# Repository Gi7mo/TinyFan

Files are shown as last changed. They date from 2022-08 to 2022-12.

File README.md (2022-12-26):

# Klipper TinyFan

### Navigation:
|[• Installation & Klipper](./Klipper)|[• Get a PCB](./PCB)|[• Mounts](./STL)|
|---|---|---|

|[• CAD Files](./CAD)|[• Manual](./TinyFan_Pinout.pdf)|[• Pictures](./Images)|
|---|---|---|
<br>

**ATTENTION**<br>
The LDO is flipped in the image, please don't mount it with the fin outward the pcb<br>
it must be mounted inward, so 180° flipped to shown in the image
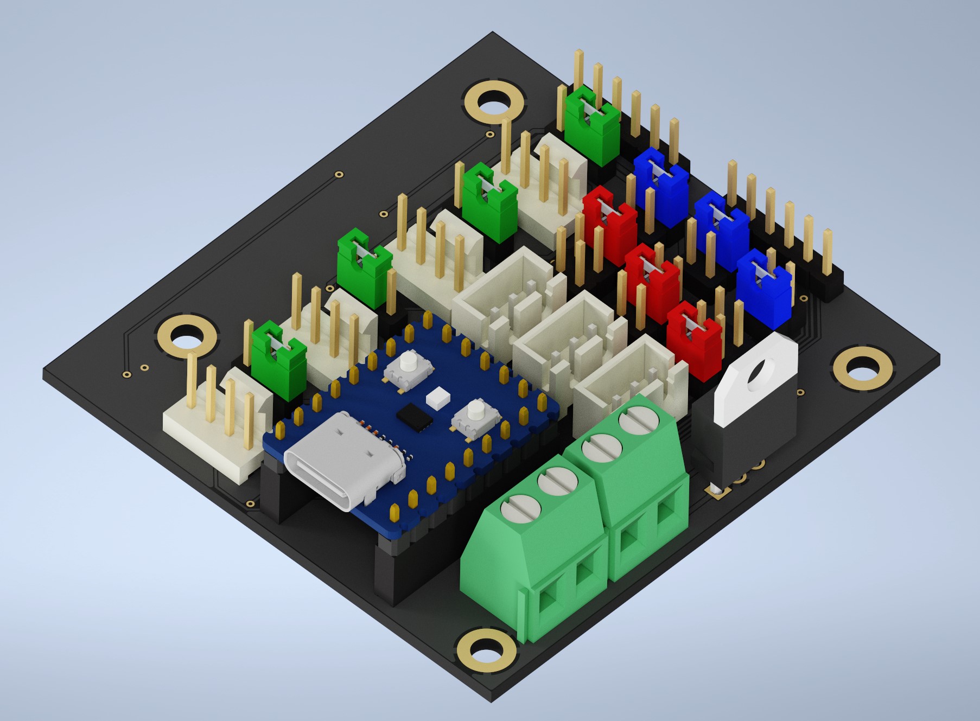
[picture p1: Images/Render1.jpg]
PCB

<br>

## Notes
- Many thanks to [Rama](https://github.com/Ramalama2) who came up with the initial idea and supported me a lot.
- You can contact me via Discord "Gi7mo!#4618"
- This project does not come with any warranty, if you choose to build/use one, you are doing this at your own risk!

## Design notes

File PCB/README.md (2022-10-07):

## TinyFan PCB Sources:
- KiCad Folder: Sources
- ProductionFiles Folder: Gerber, PNP & BOM for ordering.

## BOM:
|Reference |Quantity|Value |LCSC |Ali|
|---|---|---|---|-----|
|5VIN1 24VIN1 |2 |Conn_01x02 |C475092 |[Link](https://s.click.aliexpress.com/e/_DC1TC2L)|
|AUX1 AUX2 AUX3 |3 |Conn_01x03 |C144394 |[Link](https://s.click.aliexpress.com/e/_DEyuBIn)|
|AUX1PWR1 AUX2PWR1 AUX3PWR1 |3 |Conn_02x03_Odd_Even|C492420 |[Link](https://s.click.aliexpress.com/e/_DDO0FkL)|
|C1 C2 |2 |10pF |C107172 |[Link](https://s.click.aliexpress.com/e/_DkweKyn)|
|FAN1 FAN2 FAN3 FAN4 |4 |Conn_01x04 |C402778 | |
|FAN1PWR1 FAN2PWR1 FAN3PWR1 FAN4PWR1 |4 |Conn_01x03 |C2937625|[Link](https://s.click.aliexpress.com/e/_DDO0FkL)|
|J1 J2 J3 |3 |Conn_02x02_Odd_Even|C706892 |[Link](https://s.click.aliexpress.com/e/_DDO0FkL)|
|J4 J5 |2 |Conn_01x06_Male |C492405 |[Link](https://s.click.aliexpress.com/e/_DDO0FkL)|
|Q1 Q2 Q3 Q4 |4 |BSS138 |C52895  |[Link](https://s.click.aliexpress.com/e/_DF4Oc0f)|
|Q8 Q9 Q10 |3 |wsf3085 |C148428 |[Link](https://s.click.aliexpress.com/e/_DlBoAQT)|
|R1 R2 R3 R4 R5 R6 R7 R8 R15 R16 R17 |11 |10K |C144471 |[Link](https://s.click.aliexpress.com/e/_Ddns0gR)|
|U1 |1 |L7812 |C105651 |[Link](https://s.click.aliexpress.com/e/_DdftV8F)|
|RP2040 9Pin Female Headers |2 |9 |C39576  |[Link](https://s.click.aliexpress.com/e/_DdUyVnt)|
|RP2040 5Pin Female Headers |1 |5 |C50950  |[Link](https://s.click.aliexpress.com/e/_DFuppTv)|

Additional a [RP2040-Zero](https://s.click.aliexpress.com/e/_DFCoOxH)

**Assembly**
- Order the pcb at e.g. [pcbway](https://www.pcbway.com/project/shareproject/Voron_TinyFan_Adapter_1928b94a.html) or [jlcpcb](https://jlcpcb.com/)
- Order the parts at e.g. [lcsc](https://www.lcsc.com/)

**ATTENTION**<br>
The LDO is flipped in the image, please don't mount it with the fin outward the pcb<br>
it must be mounted inward, so 180° flipped to shown in the image
- PCB

## Notes
- This readme file contains Amazon Associate, Aliexpress affiliate, PCBWay affiliate links. I make a comission on qualifying purchases.

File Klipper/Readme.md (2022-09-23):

## Klipper:
<br>

<ul><li><details>
<summary><h3><a href="./TinyFan.cfg">TinyFan Example Config</a></h></summary>
</details></li></ul>

<ul><li><details>
<summary><h3>Board Aliases:</h></summary>
<pre>[mcu tinyfan]<br>serial: /dev/serial/by-id/usb-Klipper_rp2040_XXXXXXXXXXXX<br>restart_method: command<br><br>[board_pins tinyfan]<br>mcu: tinyfan<br>aliases:<br>	#FAN Ports:<br>	FAN1_PWM=gpio0, FAN1_RPM=gpio7,<br>	FAN2_PWM=gpio1, FAN2_RPM=gpio8,<br>	FAN3_PWM=gpio2, FAN3_RPM=gpio9,<br>	FAN4_PWM=gpio3, FAN4_RPM=gpio10,<br>	<br>	#AUX Ports:<br>	AUX1_PWM=gpio4, AUX1_RPM=gpio26,<br>	AUX2_PWM=gpio5, AUX2_RPM=gpio27,<br>	AUX3_PWM=gpio6, AUX3_RPM=gpio28,<br>	<br>	#GPIO Header:<br>	G1=gpio29, G2=gpio11, G3=gpio12,<br>	G4=gpio13, G5=gpio14, G6=gpio15,<br>	<br>	#Waveshare LED:<br>	LED=gpio16</pre>
</details></li></ul>

<ul><li>
<details>
 <summary><h3>Installation Steps:</h></summary>
 <li>ssh into your raspberry pi</li>
 <li>stop the klipper service <code>sudo systemctl stop klipper</code></li>
 <li>run <code>ls /dev</code> and keep the list open</li>
 <li>Connect the rp2040 to your raspberry while holding down the boot button</li>
 <li>run again <code>ls /dev</code> and look out for the added device, usually this is sda1</li>
 <li>chroot into your klipper directory <code>cd klipper</code></li>
 <li>cleanup all previous build files <code>make clean</code></li>
 <li>create a new build config <code>make menuconfig</code></li>
 <li>using the following settings</li>
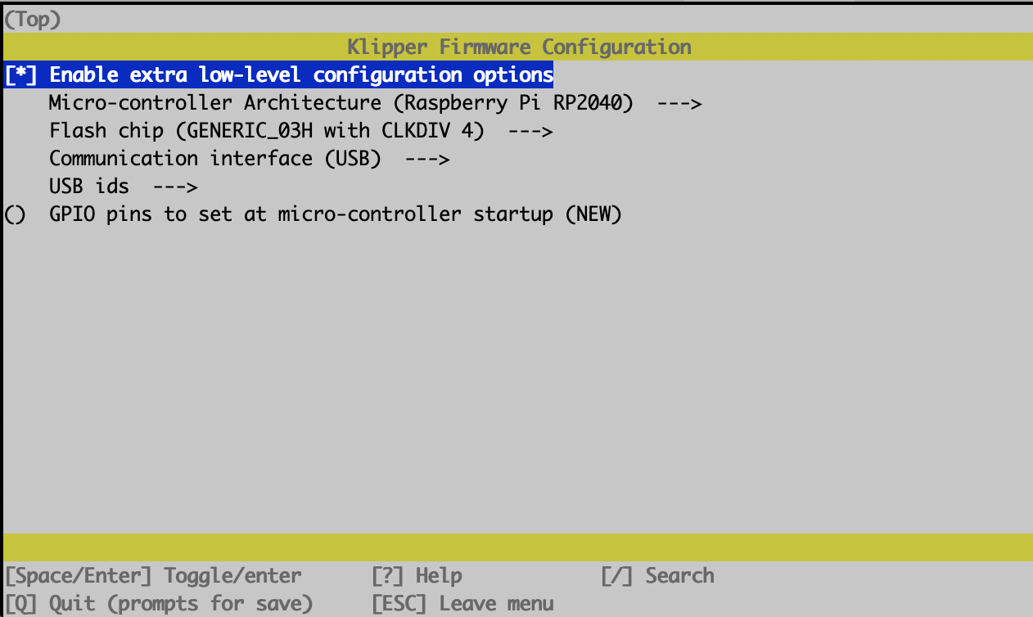
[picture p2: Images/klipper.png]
 
 <li>run the build <code>make</code></li>
 <li>copy the firmware onto the rp2040</li>
 <pre>sudo mount /dev/sda1 /mnt<br>sudo cp out/klipper.uf2 /mnt<br>sudo umount /mnt</pre>
 <li>find your mcu address by running <code>ls /dev/serial/by-id/*</code></li>
 <li>add the new mcu to your printer.cfg</li>
 <pre>[mcu fans]<br>serial: /dev/serial/by-id/usb-Klipper_rp2040_XXXX</pre>
 <li>start the klipper service <code>sudo systemctl start klipper</code></li>
</details></li></ul>

<ul><li>
<details>
 <summary><h3>Alternative Installation:</h></summary>
 <li>ssh into your raspberry pi</li>
 <li>Connect the rp2040 to your raspberry while holding down the boot button</li>
 <li>stop the klipper service <code>sudo systemctl stop klipper</code></li>
 <li>chroot into your klipper directory <code>cd klipper</code></li>
 <li>cleanup all previous build files <code>make clean</code></li>
 <li>create a new build config <code>make menuconfig</code></li>
 <li>using the following settings</li>
 
 <li>run the build <code>make</code></li>
 <li>run <code>make flash FLASH_DEVICE="2e8a:0003"</code></li>
 <li>find your mcu address by running <code>ls /dev/serial/by-id/*</code></li>
 <li>add the new mcu to your printer.cfg</li>
 <pre>[mcu fans]<br>serial: /dev/serial/by-id/usb-Klipper_rp2040_XXXX</pre>
 <li>start the klipper service <code>sudo systemctl start klipper</code></li>
</details>
</li></ul>

<ul><li>
<details>
 <summary><h3>Outputs and Options:</h></summary>
 <details>
  <summary><h4>Fan1, Fan2, Fan3 and Fan4 are PWM Fans with RPM Output and selectable Voltage for 12 and 24V</h></summary>
  <pre>[fan_generic tinyfan_fan1]<br>pin: tinyfan:FAN1_PWM<br>tachometer_pin: ^tinyfan:FAN1_RPM<br>hardware_pwm: true<br>cycle_time: 0.00004<br><br>[fan_generic tinyfan_fan2]<br>pin: tinyfan:FAN2_PWM<br>tachometer_pin: ^tinyfan:FAN2_RPM<br>hardware_pwm: true<br>cycle_time: 0.00004<br><br>[fan_generic tinyfan_fan3]<br>pin: tinyfan:FAN3_PWM<br>tachometer_pin: ^tinyfan:FAN3_RPM<br>hardware_pwm: true<br>cycle_time: 0.00004<br><br>[fan_generic tinyfan_fan4]<br>pin: tinyfan:FAN4_PWM<br>tachometer_pin: ^tinyfan:FAN4_RPM<br>hardware_pwm: true<br>cycle_time: 0.00004</pre>
 </details>
 • Be aware that the 12V rail is only capable of a max of 1.5A<br>• Aux1, Aux2 and Aux3 are more versatile
<s>Adding more Thermistors</s>
 <details>
  <summary><h4>Driving more 5V, 12V and 24V Fans</h></summary>
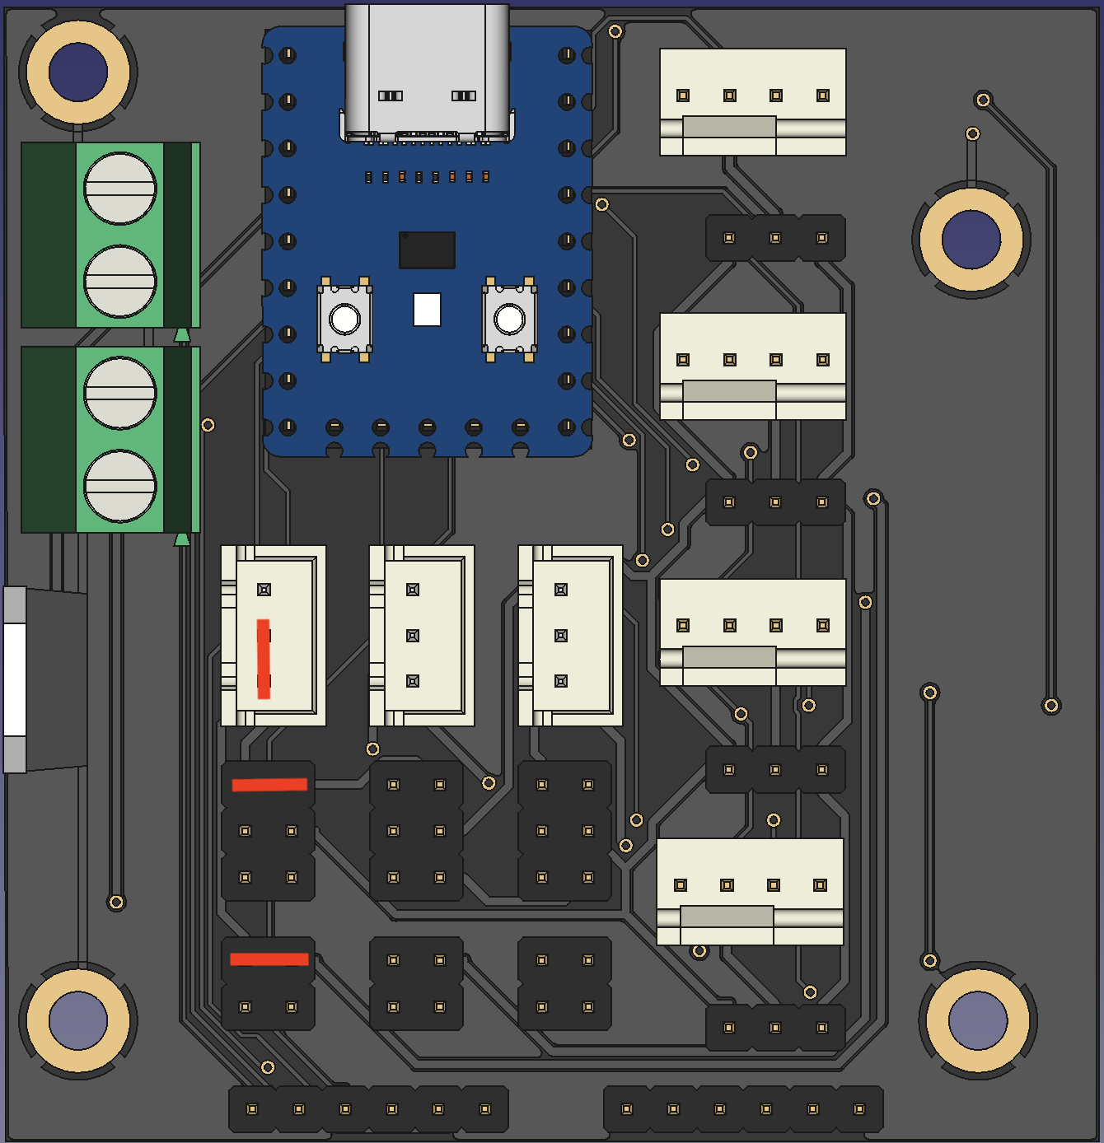
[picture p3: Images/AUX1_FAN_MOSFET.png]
  
  <pre>[fan_generic tinyfan_aux1]<br>pin: tinyfan:AUX1_PWM<br>hardware_pwm: true<br>cycle_time: 0.00004<br><br>[fan_generic tinyfan_aux2]<br>pin: tinyfan:AUX2_PWM<br>hardware_pwm: true<br>cycle_time: 0.00004<br><br>[fan_generic tinyfan_aux2]<br>pin: tinyfan:AUX3_PWM<br>hardware_pwm: true<br>cycle_time: 0.00004</pre>
 </details>
 <details>
  <summary><h4>Driving 5V, 12V and 24V Leds</h></summary>
  
  <pre>[output_pin aux1_blue]<br>pin: tinyfan:AUX1_PWM<br>pwm: True<br>cycle_time: 0.0005<br>hardware_pwm: true<br><br>[output_pin aux2_red]<br>pin: tinyfan:AUX2_PWM<br>pwm: True<br>cycle_time: 0.0005<br>hardware_pwm: true<br><br>[output_pin aux3_green]<br>pin: tinyfan:AUX3_PWM<br>pwm: True<br>cycle_time: 0.0005<br>hardware_pwm: true</pre>
 </details>
 <details>
  <summary><h4>Driving Neopixels</h></summary>
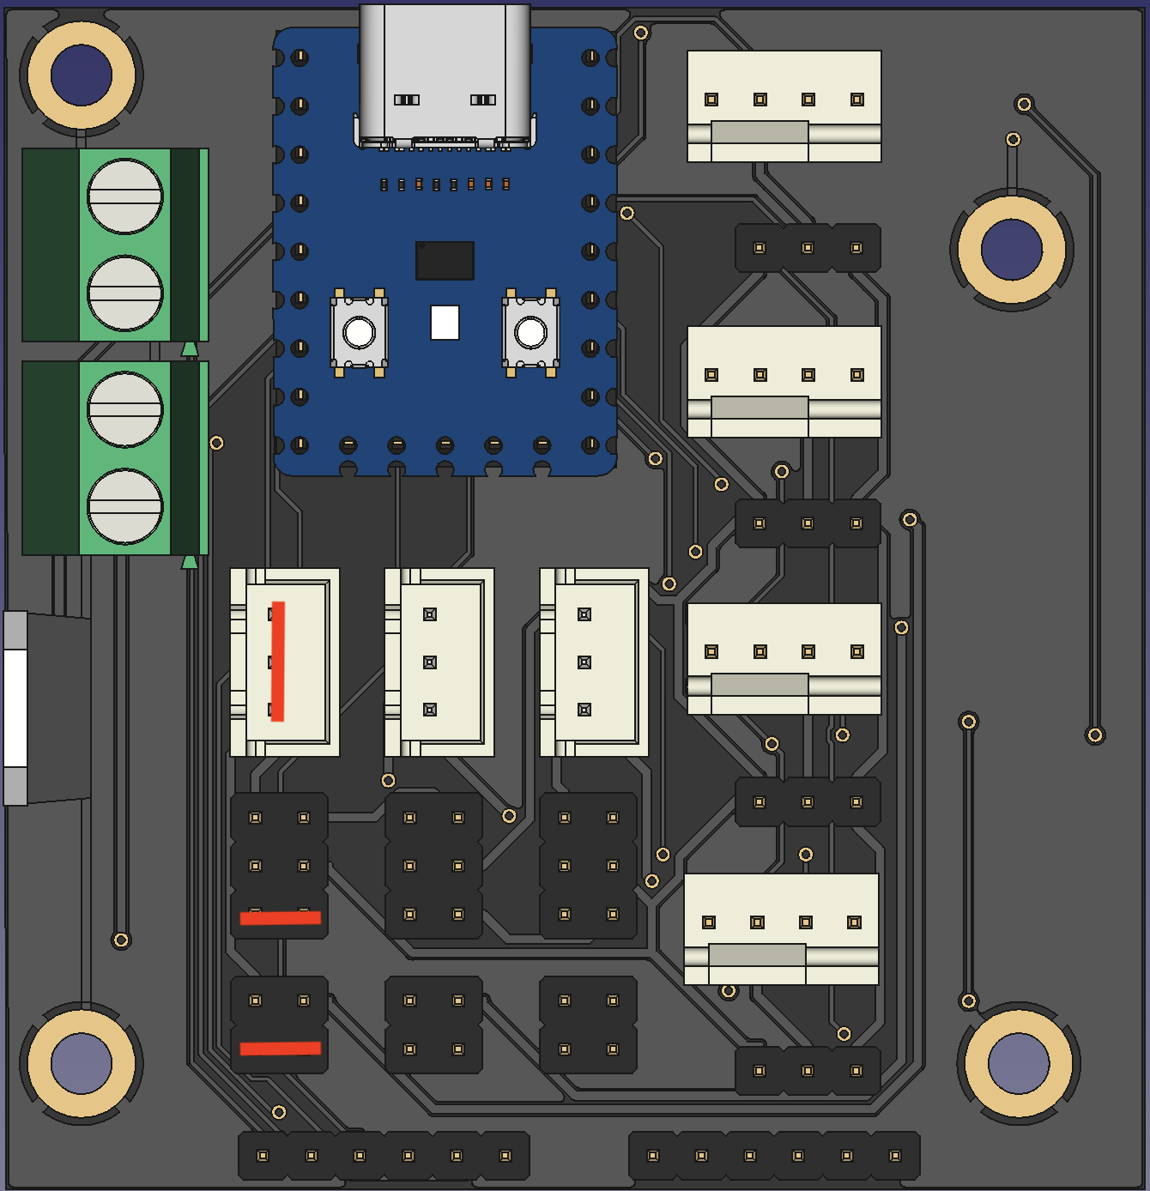
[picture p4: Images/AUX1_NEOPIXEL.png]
  
  <pre>[neopixel fan_neopixels]<br>pin: tinyfan:AUX1_RPM<br>chain_count: 18</pre>
 </details>
</details>
</li></ul>
<ul><li><details>
 <summary><h3>Pinout and Options (Picturized):</h></summary>
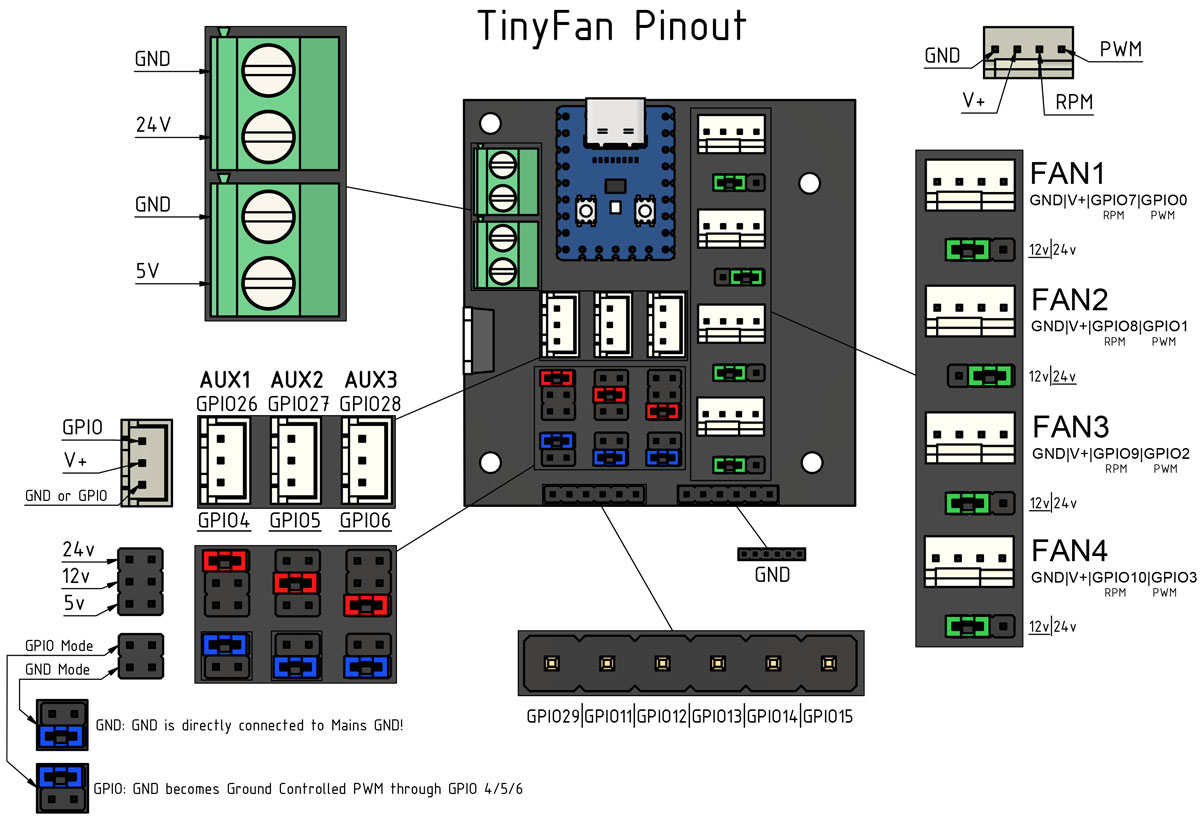
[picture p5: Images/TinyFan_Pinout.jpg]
 
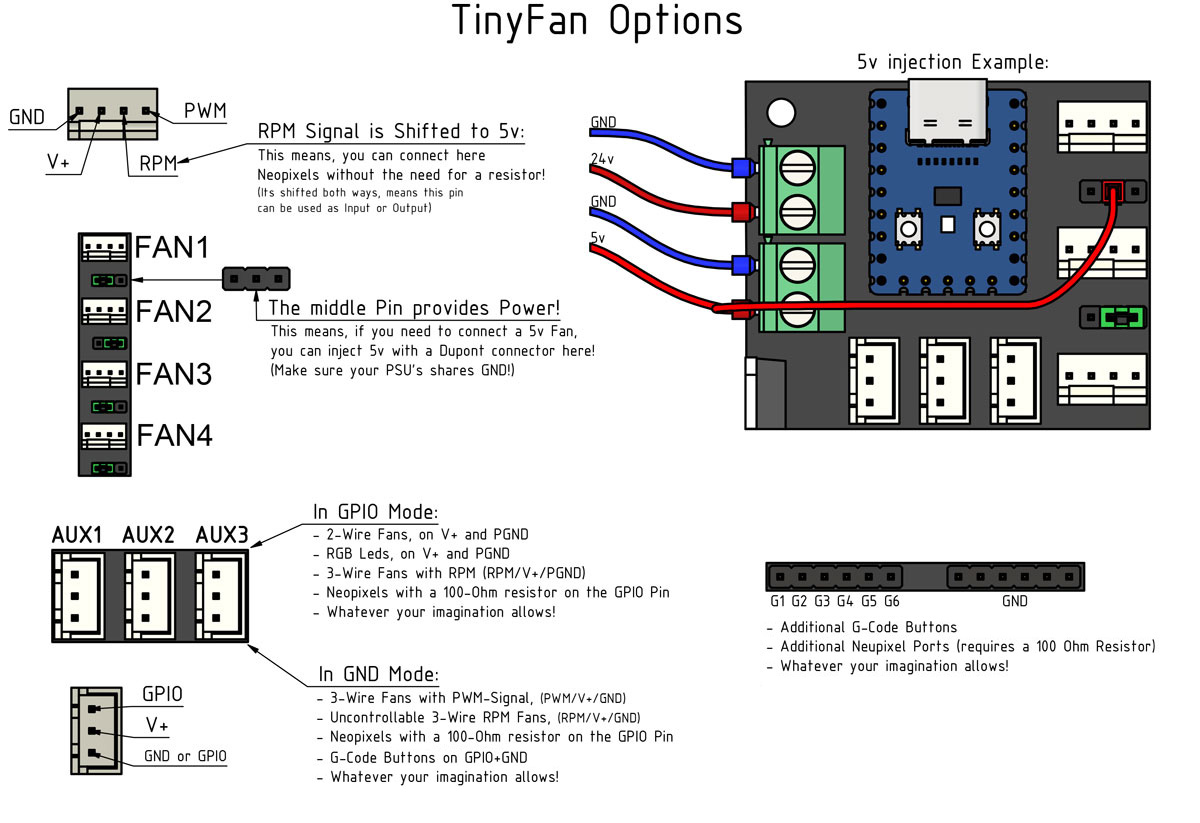
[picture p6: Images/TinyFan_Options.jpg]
 
</details></li></ul>

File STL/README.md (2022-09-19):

## Extrusion Mount:
- Folderstructure: Extrusion_DEGREE
- You can decide in which rotation you want to mount your TinyFan to the Extrusion!
- Every Folder contains a "TinyFan_Extrusion_1pc_DEGREE.stl" this one is a One Piece Version.
- Additionally there is always an Alternative Version (2 Parts) that is easier to Print! "TinyFan_Extrusion_2pc_DEGREE_A.stl" + "TinyFan_Extrusion_2pc_B.stl"
- Just as orientation Point, you will probably select the 90 degree One Piece Version.

## DIN Rail Mount:
- Consists of "TinyFan_DinRail.stl" and "New_DinClip_M3_Insert.stl"
- This one is self explanatory. See Pictures below.

## Print Settings:
- Default Voron settings, correct orientation, no supports needed!

## BOM:
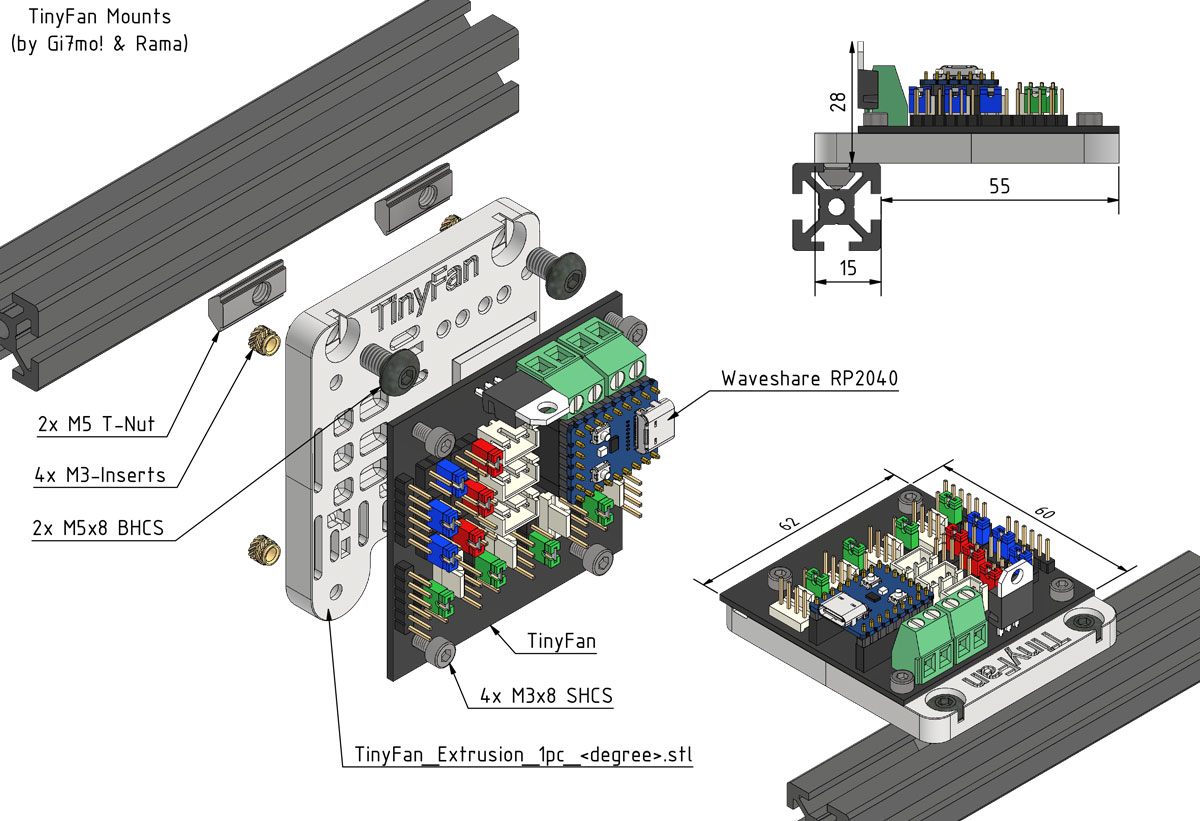
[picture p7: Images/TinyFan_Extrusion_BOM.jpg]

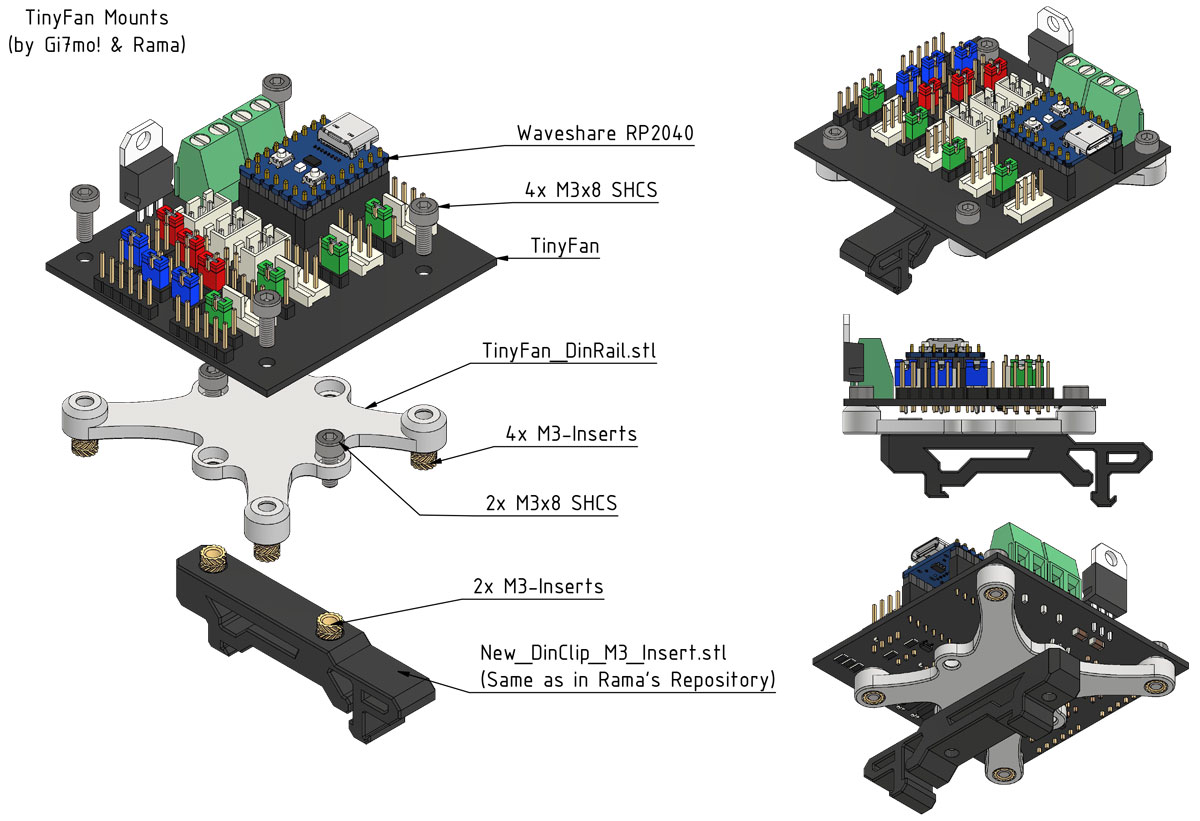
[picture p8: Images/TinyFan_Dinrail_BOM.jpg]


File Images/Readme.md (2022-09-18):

## Pictures:

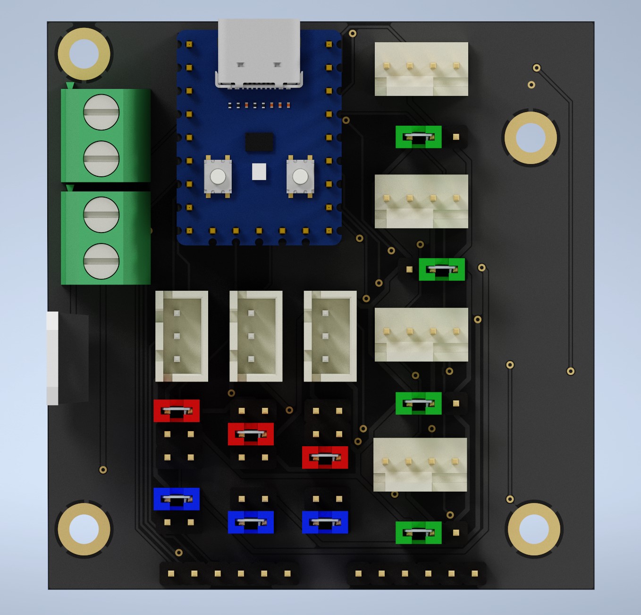
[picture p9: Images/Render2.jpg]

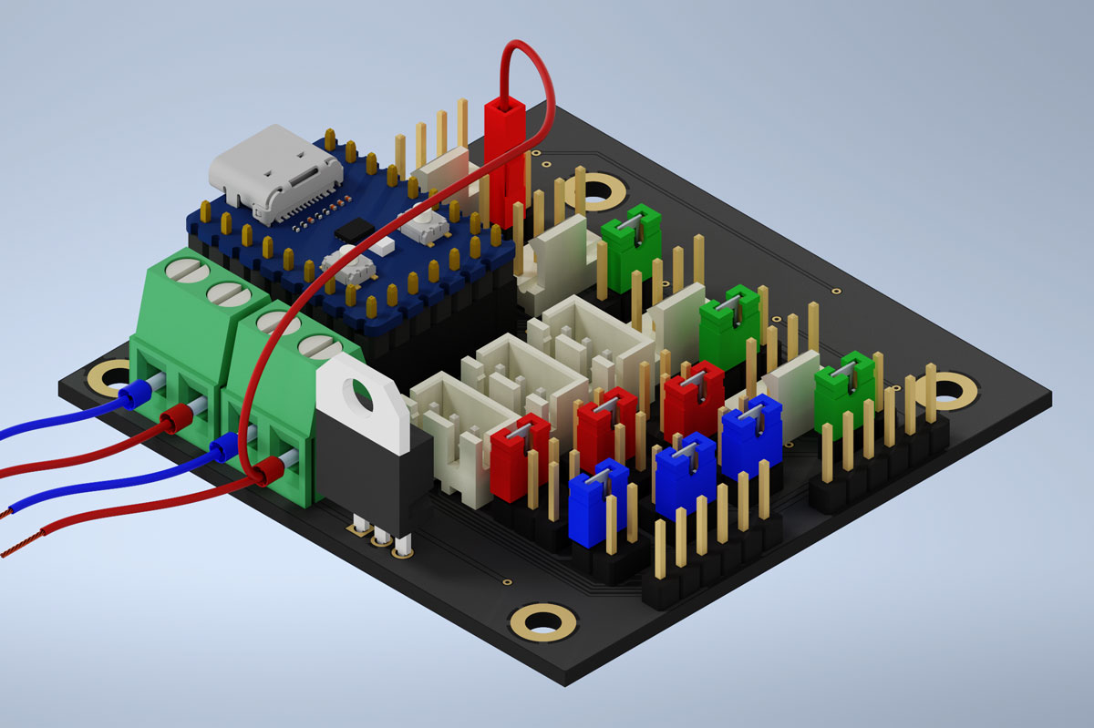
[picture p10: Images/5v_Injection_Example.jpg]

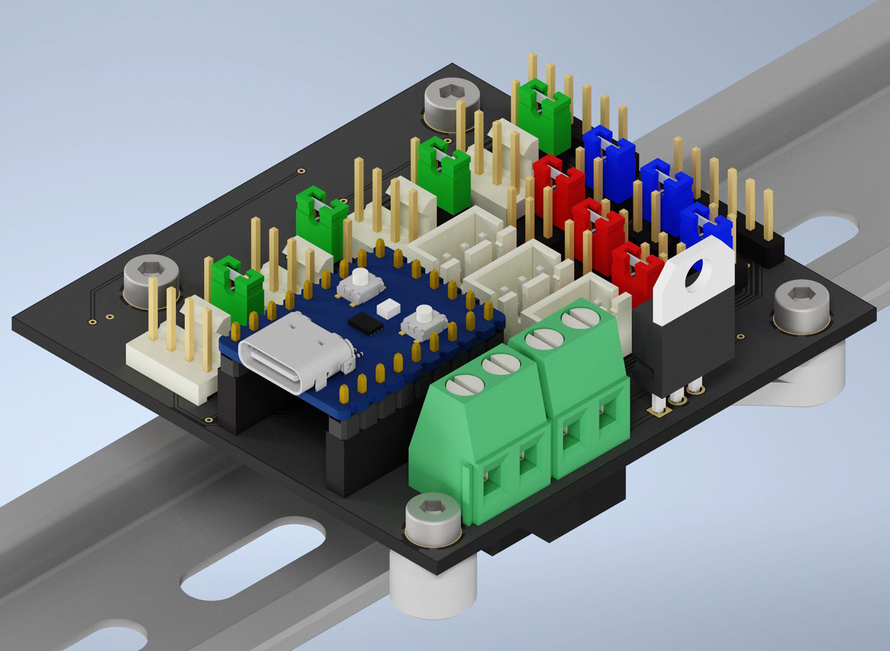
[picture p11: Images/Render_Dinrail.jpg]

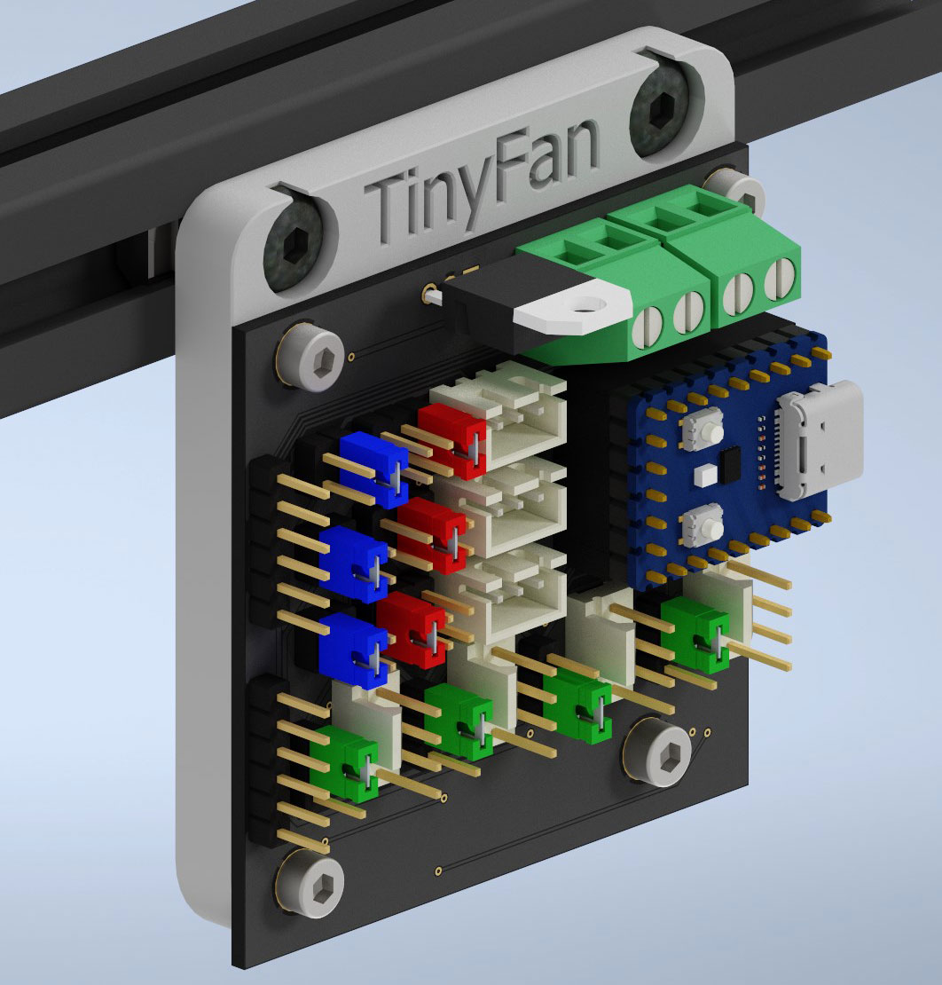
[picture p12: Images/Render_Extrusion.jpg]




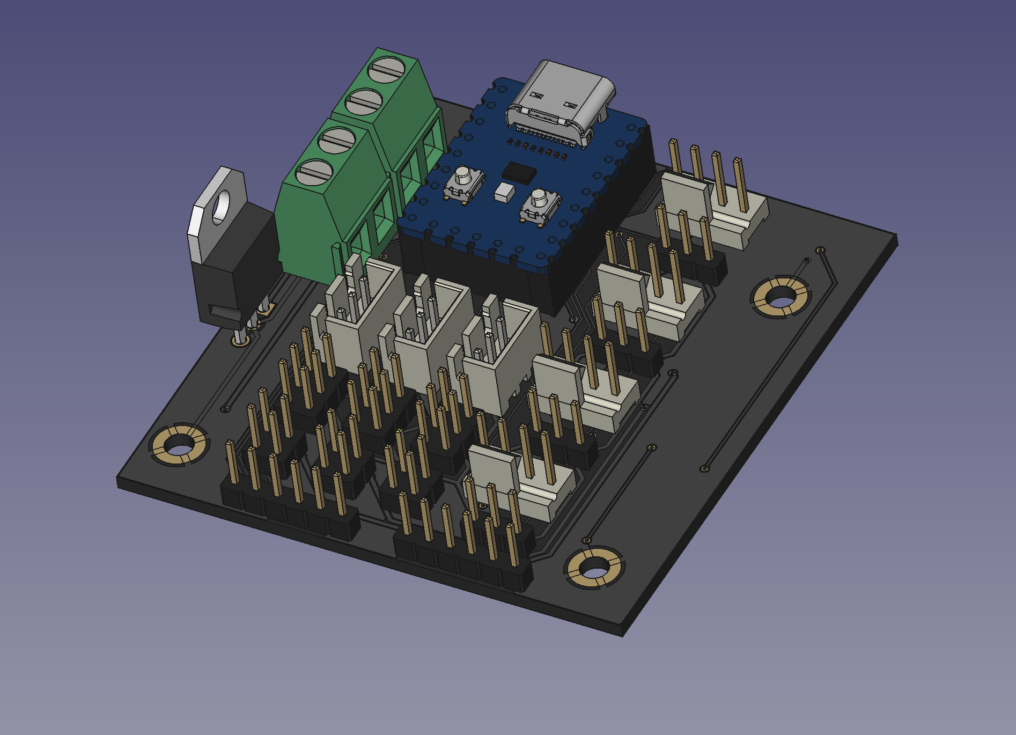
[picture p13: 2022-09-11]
Images/PCB.png

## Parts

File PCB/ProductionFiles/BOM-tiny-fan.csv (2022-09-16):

Comment | Designator | Footprint | LCSC
L7812 | U1 | TO-220-3 | C105651
10pF | C1,C2 | C_1206_3216Metric | C107172
Conn_01x03 | AUX1,AUX2,AUX3 | JST_XH_B3B-XH-AM_1x03_P2.50mm_Vertical | C144394
10K | R1,R15,R16,R17,R2,R3,R4,R5,R6,R7,R8 | R_1206_3216Metric | C144471
wsf3085 | Q10,Q8,Q9 | TO-252-2 | C148428
Conn_01x06_Male | J4 | PinHeader_1x06_P2.54mm_Vertical | C2935946
Conn_01x03 | FAN1PWR1,FAN2PWR1,FAN3PWR1,FAN4PWR1 | PinHeader_1x03_P2.54mm_Vertical | C2937625
Conn_01x04 | FAN1,FAN2,FAN3,FAN4 | FanPinHeader_1x04_P2.54mm_Vertical | C402778
Conn_01x02 | 24VIN1,5VIN1 | TerminalBlock_Phoenix_MKDS-1,5-2-5.08_1x02_P5.08mm_Horizontal | C475092
Conn_02x03_Odd_Even | AUX1PWR1,AUX2PWR1,AUX3PWR1 | PinHeader_2x03_P2.54mm_Vertical | C492420
BSS138 | Q1,Q2,Q3,Q4 | SOT-23 | C52895
Conn_02x02_Odd_Even | J1,J2,J3 | PinHeader_2x02_P2.54mm_Vertical | C706892
tiny2040 | U2 | rp2040_zero
Conn_01x06_Male | J5 | PinHeader_1x06_P2.54mm_Vertical

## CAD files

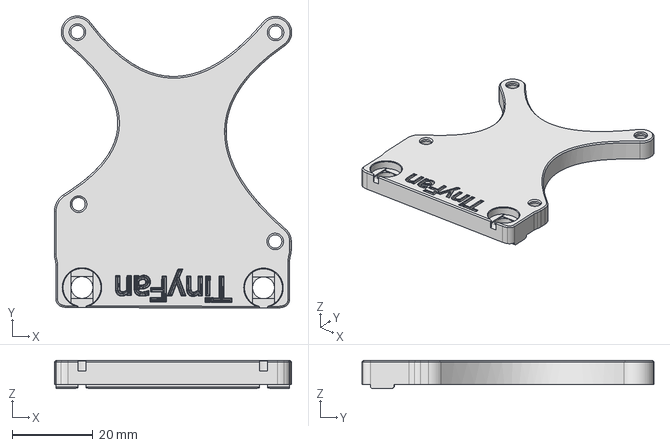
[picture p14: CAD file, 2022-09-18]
CAD/TinyFan_Extrusion_2pc_360_A.stp
58.9 x 72.4 x 7.00 mm

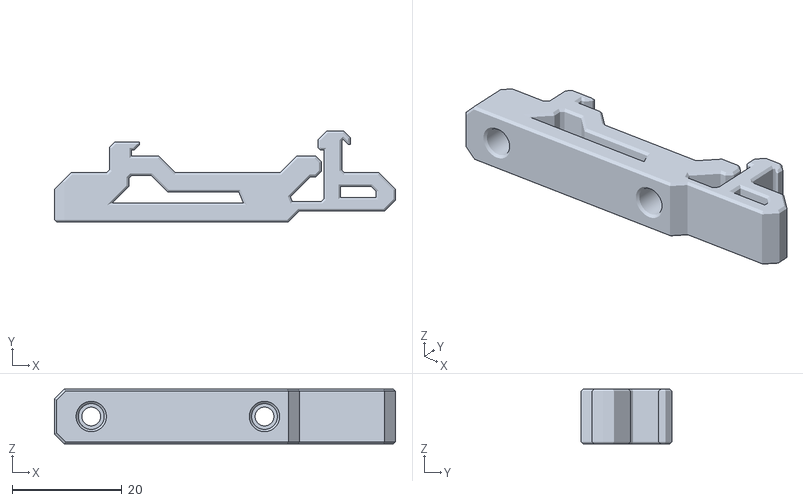
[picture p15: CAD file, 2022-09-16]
STL/New_DinClip_M3_Insert.stl
62.0 x 16.6 x 10.0

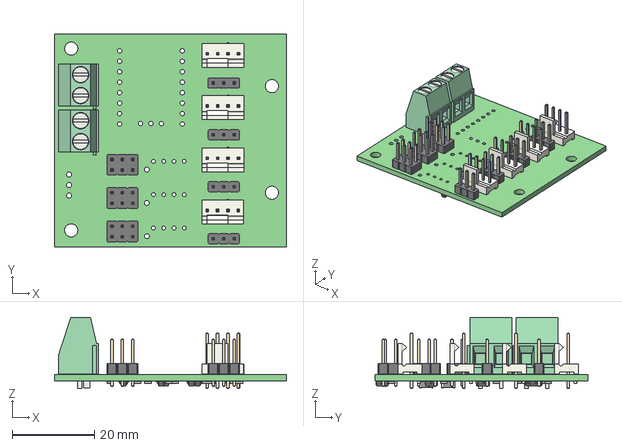
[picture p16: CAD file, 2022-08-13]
tiny-fan.step
56.4 x 51.8 x 17.3 mm
tiny-fan PCB

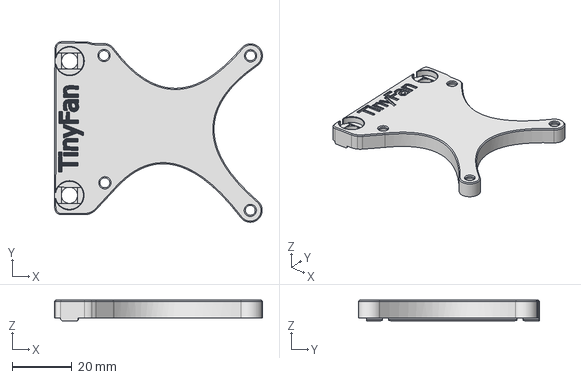
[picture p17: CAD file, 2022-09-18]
CAD/TinyFan_Extrusion_2pc_270_A.stp
69.7 x 60.5 x 7.00 mm

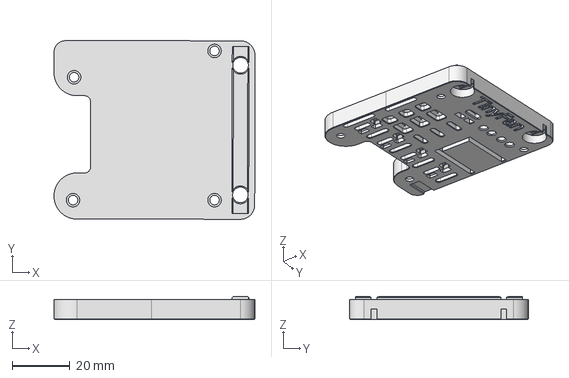
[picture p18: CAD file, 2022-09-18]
CAD/TinyFan_Extrusion_1pc_90.stp
69.8 x 62.0 x 8.00 mm

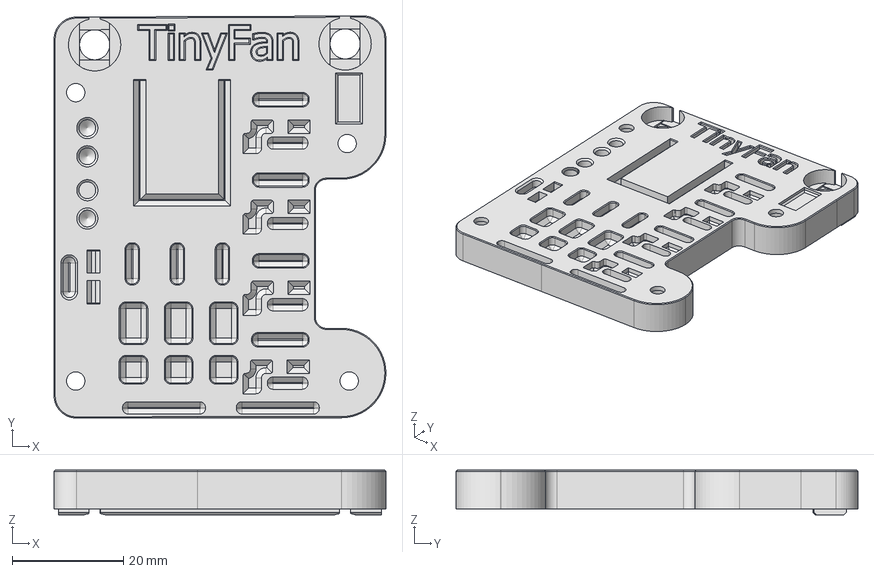
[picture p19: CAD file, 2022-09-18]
CAD/TinyFan_Extrusion_1pc_360.stp
59.6 x 72.2 x 8.00 mm

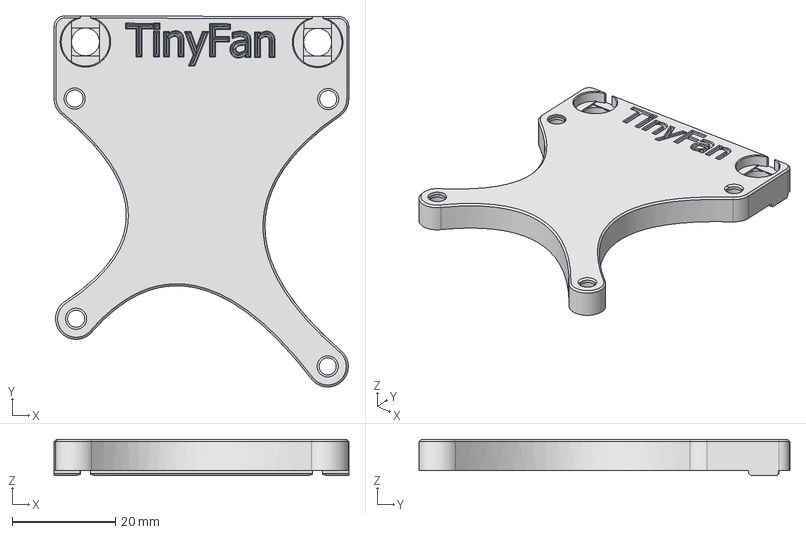
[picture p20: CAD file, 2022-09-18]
CAD/TinyFan_Extrusion_2pc_180_A.stp
57.2 x 71.9 x 7.00 mm

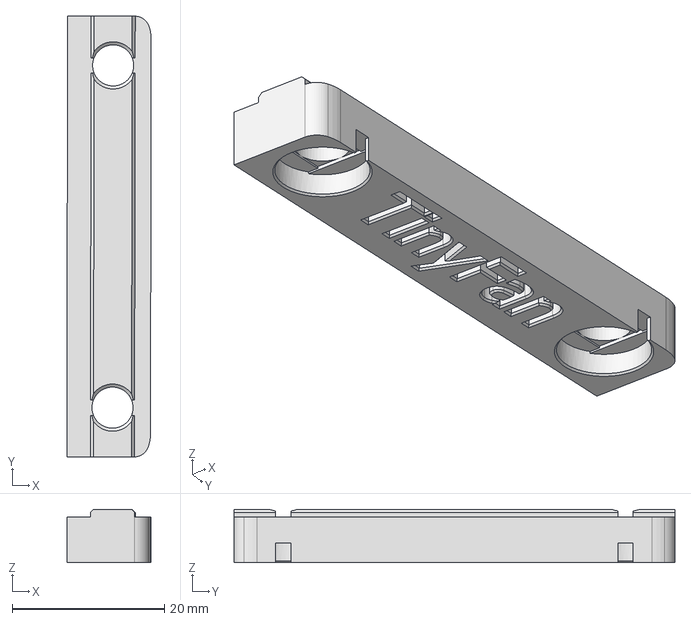
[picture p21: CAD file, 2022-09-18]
CAD/TinyFan_Extrusion_2pc_90_A_Top.stp
11.1 x 58.0 x 7.00 mm

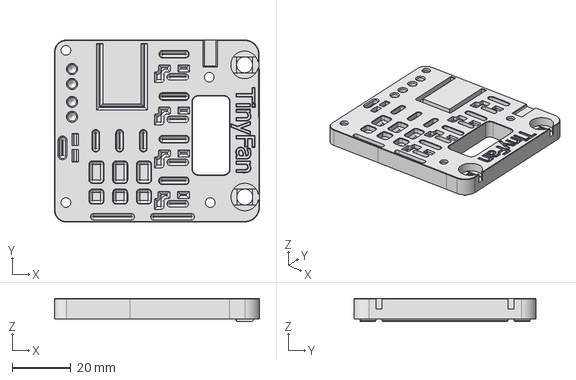
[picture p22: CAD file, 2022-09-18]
CAD/TinyFan_Extrusion_1pc_270.stp
69.8 x 62.0 x 8.00 mm

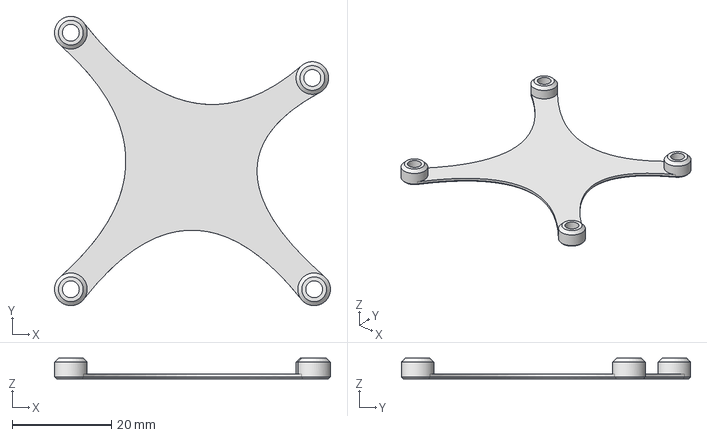
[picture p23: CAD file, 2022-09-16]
CAD/TinyFan_Extrusion_2pc_B.stp
55.7 x 58.4 x 4.20 mm

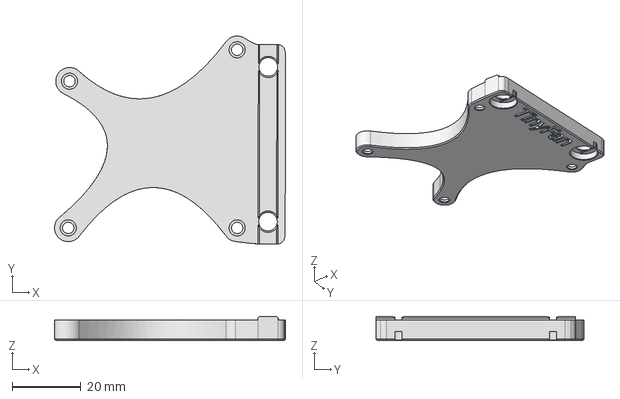
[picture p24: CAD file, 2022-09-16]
CAD/TinyFan_Extrusion_2pc_90_A.stp
67.2 x 60.5 x 7.00 mm

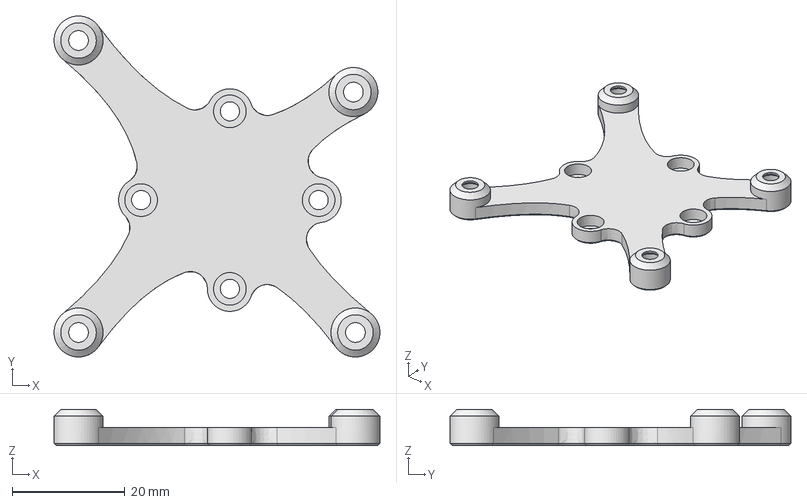
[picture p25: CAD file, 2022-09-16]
CAD/TinyFan_Dinrail.stp
57.8 x 60.5 x 6.40 mm

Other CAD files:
CAD/SRC/TinyFan_Pinout.dwg
CAD/SRC/TinyFan_Extrusion_BOM.dwg
CAD/SRC/TinyFan_Dinrail_BOM.dwg
CAD/TinyFan_Extrusion_1pc_180.stp
CAD/SRC/TinyFan_Dinrail.ipt
CAD/SRC/TinyFan_Dinrail_Assembled.iam
CAD/SRC/TinyFan_Dinrail_Explosion.iam
CAD/SRC/TinyFan_Extrusion_1pc_180.ipt
CAD/SRC/TinyFan_Extrusion_1pc_270.ipt
CAD/SRC/TinyFan_Extrusion_1pc_360.ipt
CAD/SRC/TinyFan_Extrusion_1pc_90.ipt
CAD/SRC/TinyFan_Extrusion_2pc_180_A.ipt
CAD/SRC/TinyFan_Extrusion_2pc_270_A.ipt
CAD/SRC/TinyFan_Extrusion_2pc_360_A.ipt
CAD/SRC/TinyFan_Extrusion_2pc_90_A.ipt
CAD/SRC/TinyFan_Extrusion_2pc_B.ipt
CAD/SRC/TinyFan_Extrusion_Assembled.iam
CAD/SRC/TinyFan_Extrusion_Explosion.iam
CAD/SRC/TinyFan_V2.iam
STL/TinyFan_DinRail.stl
STL/TinyFan_Extrusion_2pc_B.stl

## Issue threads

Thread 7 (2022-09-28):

What mating connector cqn I use on the FAN connectors?

GadgetAngel, 2022-09-28:
The FAN connectors on the TinyFan PCB board are PINREX 744-81-04TW20 1x4P.  What mating connector do I buy so I can wire up
my fans?

Gi7mo, 2022-09-28:
you'll need a general 4 pin pwm fan, that already has the proper connectors
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

GadgetAngel, 2022-09-28:
I found them at https://modmymods.com/mmm-4-pin-pwm-male-connector-black-mod-0112.html

Closed 2022-09-28.

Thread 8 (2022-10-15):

Everytime I reboot the Raspberry Pi the serial id for the TinyFAN PCB get lost

GadgetAngel, 2022-10-15:
Everytime I reboot the Raspberry Pi the serial id for the TinyFAN PCB get lost.  I have to hold down the "RESET" button on the RP2040 to get the serial ID to be seen by the Raspberry Pi.

Since my TinyFAN PCB is under the printer....I need a way to remotely "RESET" the RP2040-zero device

GadgetAngel, 2022-10-16:
I am implementing the TinyFAN PCB on my Voron 2.4 build to control PWM fans for my Voron build.  I have the Octopus Pro on USB-A to the Raspberry Pi 4B and the TinyFAN's RP2040-zero on port two of the USB-A of the Raspberry Pi 4B.

The instability of the USB  connection from the RP2040 device to the Raspberry Pi is due to the RP2040. See https://github.com/Klipper3d/klipper/pull/4748#issue-1013362088 :
     I quote: “RP2040 datasheet better explains the issue, but in a nutshell the USB controller requires800us of J-state(D+ high, D- low) to transition from RESET to CONNECTED. On a busy USB bus, e.g. on a single-TT hub with other 12Mbps USB
devices, this might never happen”.

Here are two work-a-rounds to this problem:

1. add a remote physical "RESET" button to the Skirt on the Voron 2.4 build
2.  install "uhubctl" on the Pi to power off and them power on the USB-A ports (basically to "RESET" the RP2040 usb-c por
       which is really a USB-A port on the Pi)

To do #1 work-a-round a couple of items are needed:
1. wire
2.  Skirt mount for a 16mm button :
3. https://github.com/hartk1213/MISC/blob/main/Voron%20Mods/Voron%202/2.4/Voron2.4_16mm_button_skirt/STLs/16mm_button_skirt_insert_front.stl
4.  I had to trim the "16mm_button_skirt_insert_front.stl" piece down with my Dremel tool so that I could use the retaining "screw on" collar that came with the 16mm momentary button I bought off of Amazon
5. buy a 16mm momentary button from of Amazon at https://www.amazon.com/dp/B01MQV6NJR
6. Hot Glue Gun and Hot Glue to secure the 16mm momentary button from of Amazon mounted on to "16mm_button_skirt_insert_front.stl" piece with the provided screw on collar.  The screw on collar will secure the button to the "16mm_button_skirt_insert_front.stl" piece but not to the skirt.  So use some hot glue to ensure the "16mm_button_skirt_insert_front.stl" piece stays on the Skirt.  I placed hot glue on the backside of the Skirt.
7.  one "Short USB-A to USB-C" cable : https://www.amazon.com/gp/product/B08933P982
8.  cut the "Short USB-A to USB-C" cable so that you can wire the 16mm button in between the cut pieces.
9.  There are 4 wires inside the "Short USB-A to USB-C" cable. Strip the cut ends to gain access to the wires.
   There is a BLACK (GND), RED (5V), GREEN (Data+) and White (Data-) wires inside. Follow the below diagram
   on how to hookup the switch between the two halves of the short USB-A to USB-C cable.

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

To do #2 work-a-round a couple of items are needed:
1. see, https://klipper.discourse.group/t/rp2040-pico-suddenly-unable-to-connect-usb-issue/2554
2. see https://funprojects.blog/2021/04/26/control-usb-powered-devices/
3. To install uhubctl:
```
       $sudo apt-get install libusb-1.0-0-dev
       $git clone https://github.com/mvp/uhubctl
       $cd uhubctl
       $make
       $sudo make install
```

GadgetAngel, 2022-10-20:
To be able to RESET the RP2040 chip on the TinyFAN PCB you will need to purchase a couple of items.  Some are stated in my previous comments but here is the list again with a Relay I purchased from Amazon.

1.buy a 16mm momentary button from of Amazon at https://www.amazon.com/dp/B01MQV6NJR
2. one "Short USB-A to USB-C" cable : https://www.amazon.com/gp/product/B08933P982
3. buy a 5V Relay from Amazon that allows for NO and NC connections: https://www.amazon.com/gp/product/B00LW15A4W

Now wire this all up as shown in the following diagram
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

Follow the instruction in "Instructions for Software RESET of RP2040 chip.txt" file
[Instructions for Software RESET of RP2040 chip.txt](https://github.com/Gi7mo/TinyFan/files/9826191/Instructions.for.Software.RESET.of.RP2040.chip.txt)

In the end, if you follow all the instructions: every time you power off the printer and turn it back on; or reboot the printer the RP2040 USB communications will be automatically reset so that when the printer finished booting up the link to the USB serial will be present.  You will also have access to a web page and additional URL so that you can control the relay via software.

You will also have access to three HTML button at URL:
http:[Your Raspberry PI IP address]:7990/resetrp2040.html

You will see the following three buttons:
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

Ramalama2, 2023-04-24:
Hey @GadgetAngel
There is actually a solution, you can simply flash the can bootloader, check the "skr pico" issue thread.
Then you can still use simply the usb connection to the pico.
Means you just need the can bootloader but you don't have to use can.

I didn't tested personally that approach, but im pretty sure it solves the issue.

Otherwise afterwards, the rp2040 wasn't the best decision with this usb bug, but there aren't any/many stm32 based alternatives.

Here is the direct link to the solution, just keep in mind that the flashchip on the waveshare is the "Generic_03H".
https://github.com/bigtreetech/SKR-Pico/issues/2#issuecomment-1500925079

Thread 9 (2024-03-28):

L7812 wrongly designated as an LDO regulator

HumbleDeer, 2024-03-28:
The 7812 is old & venerable, and not an LDO regulator. Its dropout voltage input to output is a few volts.

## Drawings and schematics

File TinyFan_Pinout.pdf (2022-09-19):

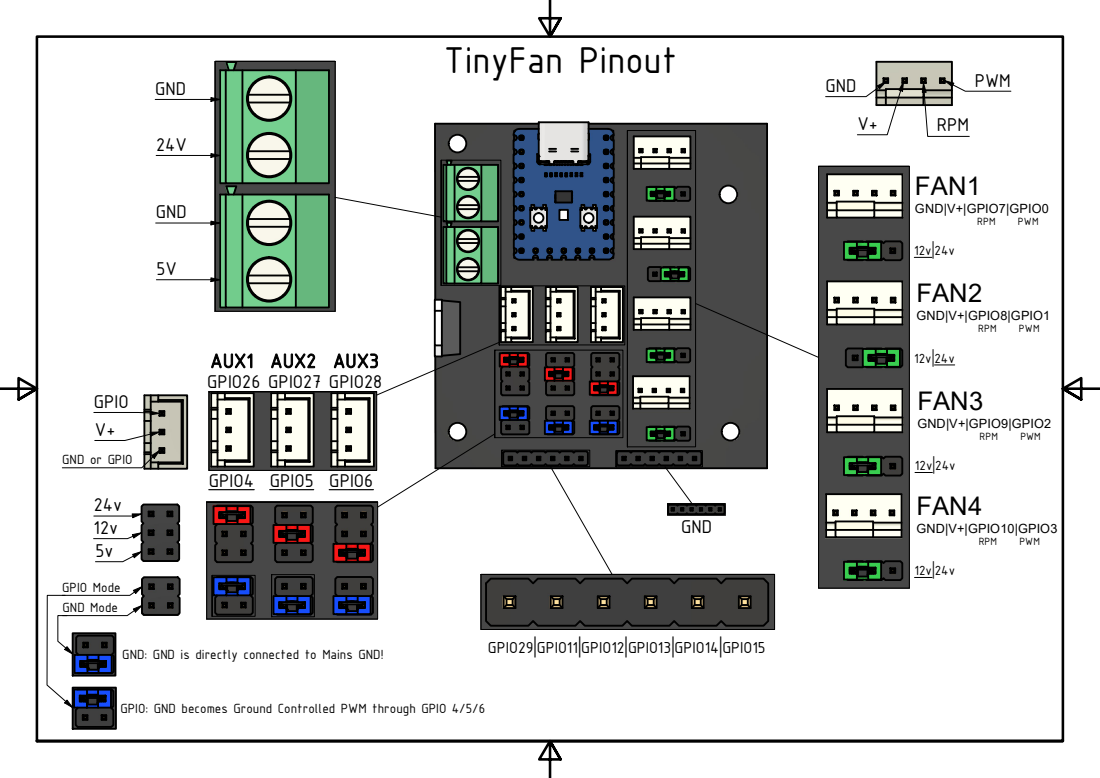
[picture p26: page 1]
GPIO26 GPIO27 GPIO28; AUX1 AUX2 AUX3; GPIO4 GPIO5 GPIO6; GPIO Mode; GND Mode; TinyFan Pinout

GND or GPIO

GND: GND is directly connected to Mains GND!

GPIO: GND becomes Ground Controlled PWM through GPIO 4/5/6

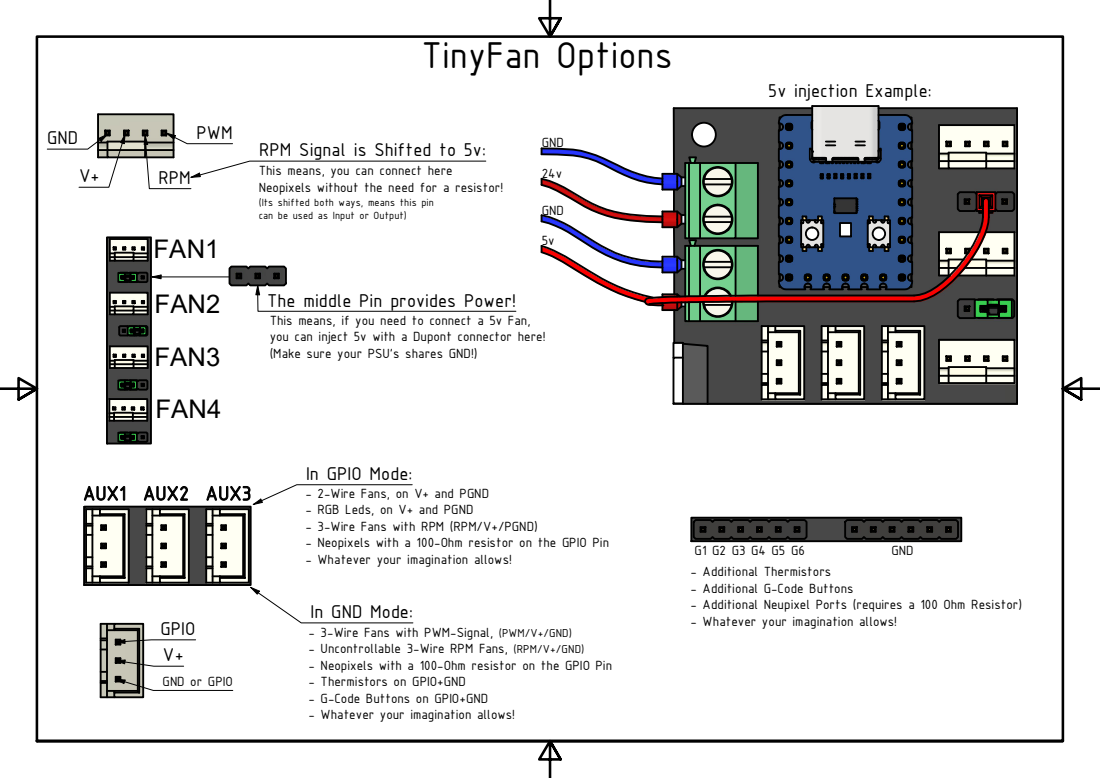
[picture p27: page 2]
TinyFan Options; AUX1 AUX2 AUX3; 5v injection Example:; GND

RPM Signal is Shifted to 5v:

This means, you can connect here
Neopixels without the need for a resistor!
(Its shifted both ways, means this pin
can be used as Input or Output)

The middle Pin provides Power!
This means, if you need to connect a 5v Fan,
you can inject 5v with a Dupont connector here!
(Make sure your PSU's shares GND!)

In GPIO Mode:
- 2-Wire Fans, on V+ and PGND
- RGB Leds, on V+ and PGND
- 3-Wire Fans with RPM (RPM/V+/PGND)
- Neopixels with a 100-Ohm resistor on the GPIO Pin
- Whatever your imagination allows!

- Additional Thermistors
- Additional G-Code Buttons
- Additional Neupixel Ports (requires a 100 Ohm Resistor)

In GND Mode:
- 3-Wire Fans with PWM-Signal, (PWM/V+/GND)
- Uncontrollable 3-Wire RPM Fans, (RPM/V+/GND)
- Thermistors on GPIO+GND
- G-Code Buttons on GPIO+GND

GND or GPIO

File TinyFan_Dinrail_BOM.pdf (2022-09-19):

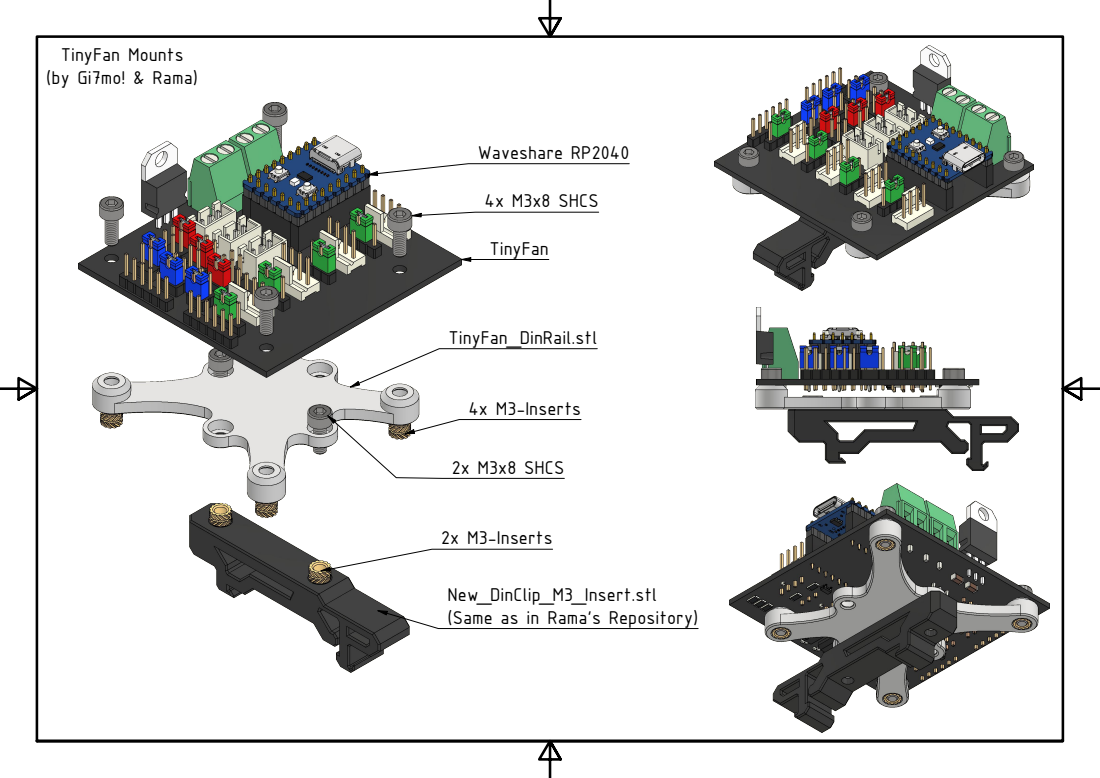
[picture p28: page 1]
4x M3-Inserts; 2x M3-Inserts; 2x M3x8 SHCS; TinyFan Mounts (by Gi7mo! & Rama); 4x M3x8 SHCS; Waveshare RP2040

New_DinClip_M3_Insert.stl
(Same as in Rama's Repository)

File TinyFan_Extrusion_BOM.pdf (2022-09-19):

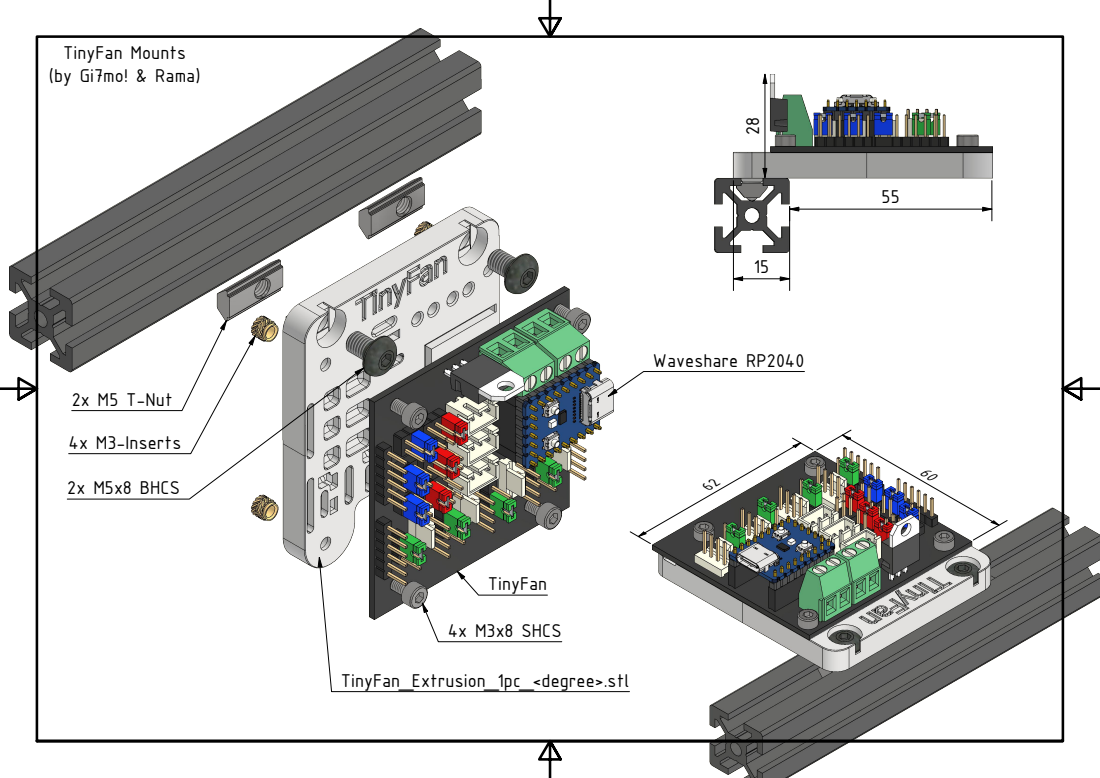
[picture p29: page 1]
2x M5x8 BHCS; 2x M5 T-Nut; 4x M3x8 SHCS; 4x M3-Inserts; Waveshare RP2040; TinyFan Mounts (by Gi7mo! & Rama)

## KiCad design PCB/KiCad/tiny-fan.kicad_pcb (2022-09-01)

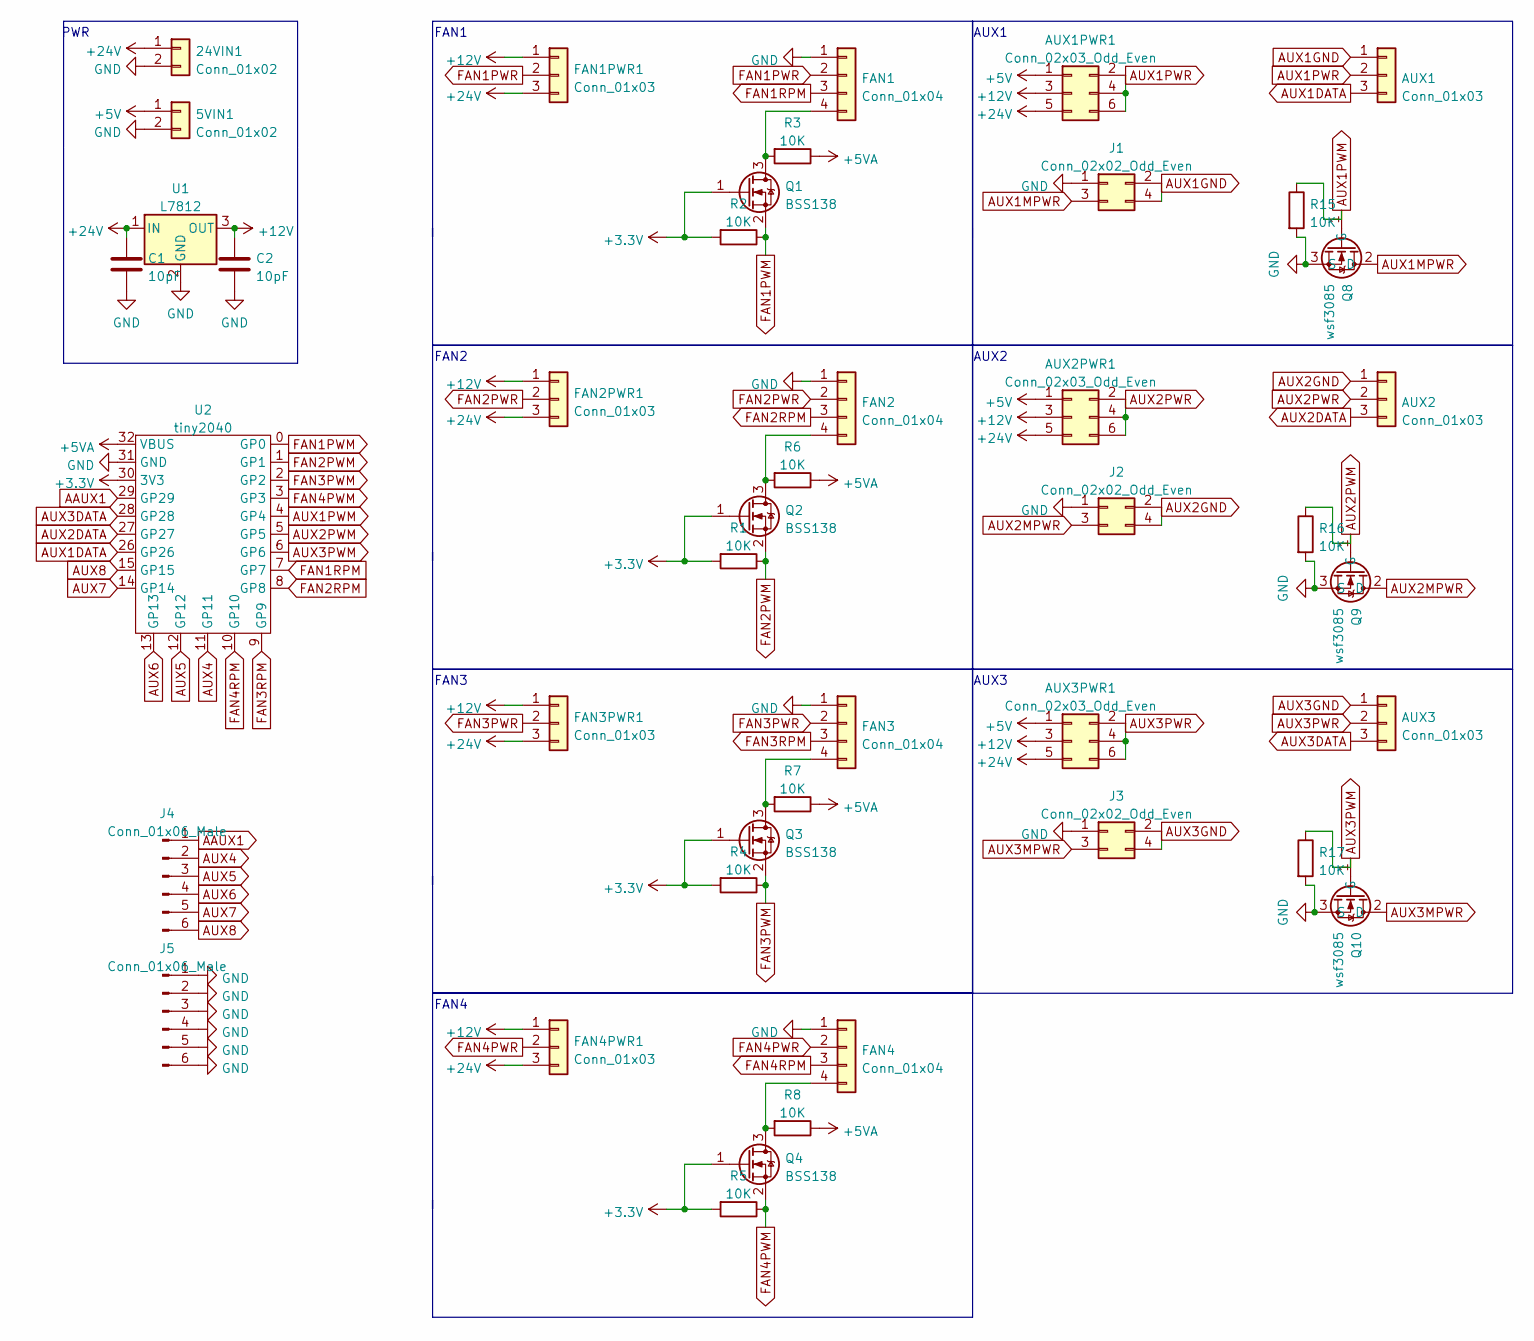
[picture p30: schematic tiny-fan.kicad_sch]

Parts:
5VIN1, 24VIN1: Conn_01x02; TerminalBlock_Phoenix_MKDS-1,5-2-5.08_1x02_P5.08mm_Horizont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; LCSC C475092
AUX1, AUX2, AUX3: Conn_01x03; JST_XH_B3B-XH-AM_1x03_P2.50mm_Vertical; LCSC C144394
AUX1PWR1, AUX2PWR1, AUX3PWR1: Conn_02x03_Odd_Even; PinHeader_2x03_P2.54mm_Vertical; LCSC C492420
C1, C2: 10pF; C_1206_3216Metric; LCSC C107172
FAN1, FAN2, FAN3, FAN4: Conn_01x04; FanPinHeader_1x04_P2.54mm_Vertical; LCSC C402778
FAN1PWR1, FAN2PWR1, FAN3PWR1, FAN4PWR1: Conn_01x03; PinHeader_1x03_P2.54mm_Vertical; LCSC C2937625
J1, J2, J3: Conn_02x02_Odd_Even; PinHeader_2x02_P2.54mm_Vertical; LCSC C706892
J4, J5: Conn_01x06_Male; PinHeader_1x06_P2.54mm_Vertical; LCSC C962326
Q1, Q2, Q3, Q4: BSS138; SOT-23; LCSC C52895
Q8, Q9, Q10: wsf3085; TO-252-2; LCSC C148428
R1, R2, R3, R4, R5, R6, R7, R8, R15, R16, R17: 10K; R_1206_3216Metric; LCSC C144471
U1: L7812; TO-220-3; LCSC C105651
U2: tiny2040; rp2040_zero

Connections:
+3V3: Q1.1 (G), Q2.1 (G), Q3.1 (G), Q4.1 (G), R1.2, R2.2, R4.2, R5.2, U2.30 (3V3)
+5V: 5VIN1.1, AUX1PWR1.1, AUX2PWR1.1, AUX3PWR1.1
+5VA: R3.1, R6.1, R7.1, R8.1, U2.32 (VBUS)
+12V: AUX1PWR1.3, AUX2PWR1.3, AUX3PWR1.3, C2.1, FAN1PWR1.1, FAN2PWR1.1, FAN3PWR1.1, FAN4PWR1.1, U1.3 (OUT)
+24V: 24VIN1.1, AUX1PWR1.5, AUX2PWR1.5, AUX3PWR1.5, C1.1, FAN1PWR1.3, FAN2PWR1.3, FAN3PWR1.3, FAN4PWR1.3, U1.1 (IN)
AAUX1: J4.1, U2.29 (GP29)
AUX1DATA: AUX1.3, U2.26 (GP26)
AUX1GND: AUX1.1, J1.2, J1.4
AUX1MPWR: J1.3, Q8.2 (D)
AUX1PWM: Q8.1 (G), R15.1, U2.4 (GP4)
AUX1PWR: AUX1.2, AUX1PWR1.2, AUX1PWR1.4, AUX1PWR1.6
AUX2DATA: AUX2.3, U2.27 (GP27)
AUX2GND: AUX2.1, J2.2, J2.4
AUX2MPWR: J2.3, Q9.2 (D)
AUX2PWM: Q9.1 (G), R16.1, U2.5 (GP5)
AUX2PWR: AUX2.2, AUX2PWR1.2, AUX2PWR1.4, AUX2PWR1.6
AUX3DATA: AUX3.3, U2.28 (GP28)
AUX3GND: AUX3.1, J3.2, J3.4
AUX3MPWR: J3.3, Q10.2 (D)
AUX3PWM: Q10.1 (G), R17.1, U2.6 (GP6)
AUX3PWR: AUX3.2, AUX3PWR1.2, AUX3PWR1.4, AUX3PWR1.6
AUX4: J4.2, U2.11 (GP11)
AUX5: J4.3, U2.12 (GP12)
AUX6: J4.4, U2.13 (GP13)
AUX7: J4.5, U2.14 (GP14)
AUX8: J4.6, U2.15 (GP15)
FAN1PWM: Q1.2 (S), R2.1, U2.0 (GP0)
FAN1PWR: FAN1.2, FAN1PWR1.2
FAN1RPM: FAN1.3, U2.7 (GP7)
FAN2PWM: Q2.2 (S), R1.1, U2.1 (GP1)
FAN2PWR: FAN2.2, FAN2PWR1.2
FAN2RPM: FAN2.3, U2.8 (GP8)
FAN3PWM: Q3.2 (S), R4.1, U2.2 (GP2)
FAN3PWR: FAN3.2, FAN3PWR1.2
FAN3RPM: FAN3.3, U2.9 (GP9)
FAN4PWM: Q4.2 (S), R5.1, U2.3 (GP3)
FAN4PWR: FAN4.2, FAN4PWR1.2
FAN4RPM: FAN4.3, U2.10 (GP10)
GND: 5VIN1.2, 24VIN1.2, C1.2, C2.2, FAN1.1, FAN2.1, FAN3.1, FAN4.1, J1.1, J2.1, J3.1, J5.1, J5.2, J5.3, J5.4, J5.5, J5.6, Q8.3 (S), Q9.3 (S), Q10.3 (S), R15.2, R16.2, R17.2, U1.2 (GND), U2.31 (GND); also elsewhere on the board
unnamed: FAN1.4, Q1.3 (D), R3.2
unnamed: FAN2.4, Q2.3 (D), R6.2
unnamed: FAN3.4, Q3.3 (D), R7.2
unnamed: FAN4.4, Q4.3 (D), R8.2

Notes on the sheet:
AUX3
FAN1
AUX1
AUX2
FAN4
FAN3
FAN2
PWR

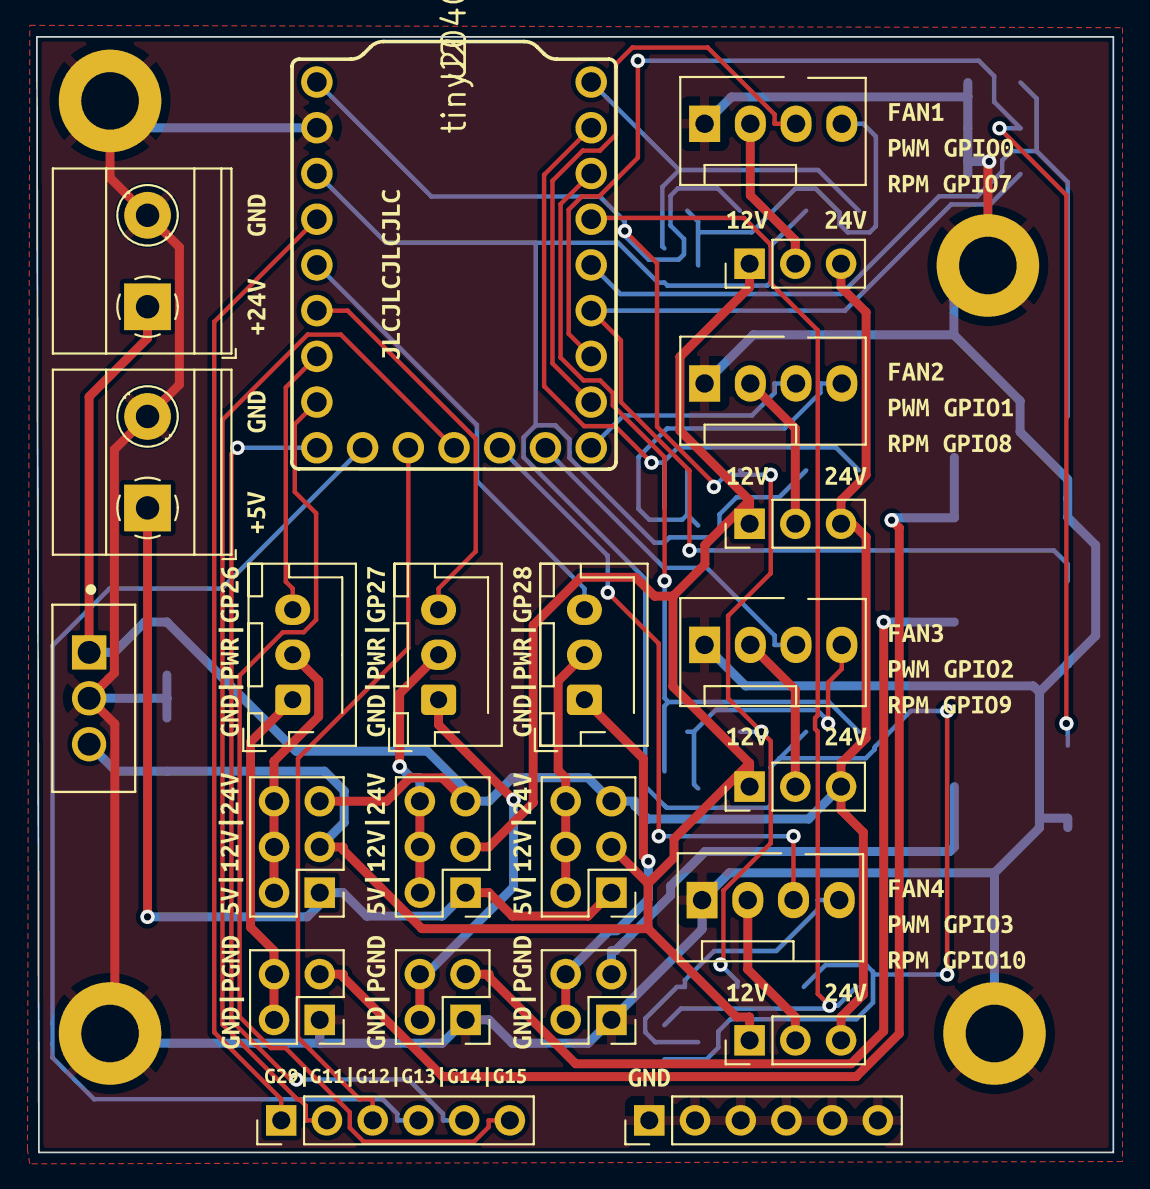
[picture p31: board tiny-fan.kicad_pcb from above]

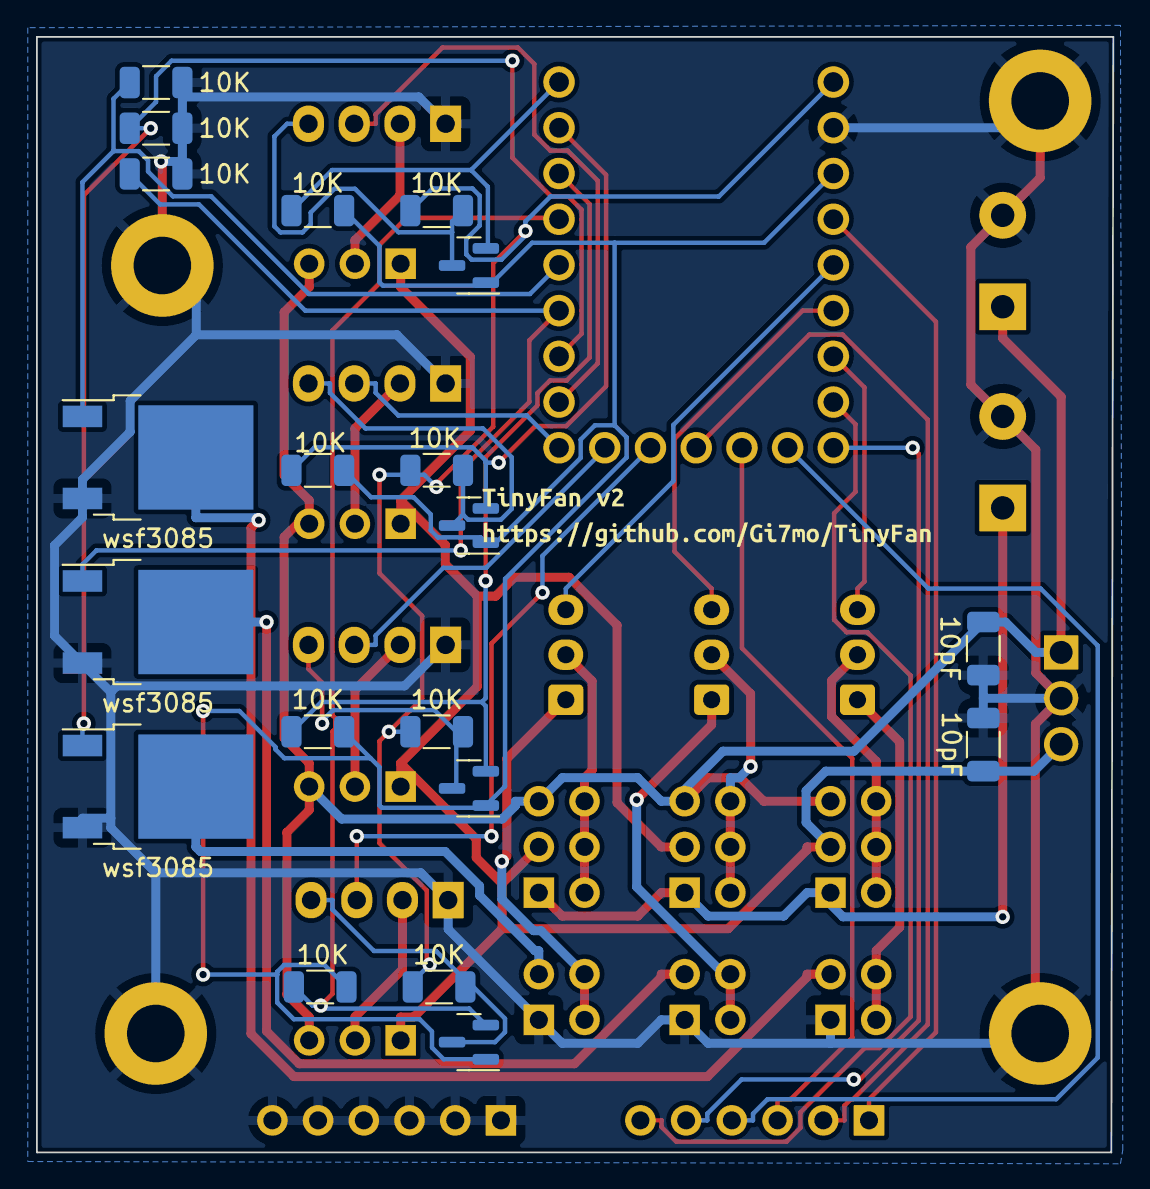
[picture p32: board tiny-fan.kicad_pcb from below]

Board: 2 copper layers, 59.8 x 62.0 mm, 76 parts (21 on the bottom side), 43 nets.

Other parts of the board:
REF1, REF2, REF3, REF4: MountingHole_3.2mm_M3_ISO7380_Pad
kibuzzard-62F4AAD2: G***; kibuzzard-62F4AAD2
kibuzzard-62F425A2: G***; kibuzzard-62F425A2
kibuzzard-62F425B31: G***; kibuzzard-62F425B3
kibuzzard-62F425BF: G***; kibuzzard-62F425BF
kibuzzard-62F894BF: G***; kibuzzard-62F894BF
kibuzzard-62F894CE: G***; kibuzzard-62F894CE
kibuzzard-62F894DE: G***; kibuzzard-62F894DE
kibuzzard-62F4287A, kibuzzard-62F4287AA, kibuzzard-62F4287AB, kibuzzard-62F4287AC: G***; kibuzzard-62F4287A
kibuzzard-62F42591: G***; kibuzzard-62F42591
kibuzzard-62F42661, kibuzzard-62F426612, kibuzzard-62F426613: G***; kibuzzard-62F42661
kibuzzard-62F42888, kibuzzard-62F428881, kibuzzard-62F428884, kibuzzard-62F4288845: G***; kibuzzard-62F42888
kibuzzard-630F90A1: G***; kibuzzard-630F90A1
kibuzzard-630F902C: G***; kibuzzard-630F902C
kibuzzard-630F922D: G***; kibuzzard-630F922D
kibuzzard-630F9081: G***; kibuzzard-630F9081
kibuzzard-630F9093: G***; kibuzzard-630F9093
kibuzzard-630F9163: G***; kibuzzard-630F9163
kibuzzard-630F9189: G***; kibuzzard-630F9189
kibuzzard-630F9193: G***; kibuzzard-630F9193
kibuzzard-631047F8: G***; kibuzzard-631047F8
kibuzzard-63104730: G***; kibuzzard-63104730

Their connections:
GND: REF1.1, REF2.1, REF3.1, REF4.1; also elsewhere on the board

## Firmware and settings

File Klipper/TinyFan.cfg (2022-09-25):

[mcu tinyfan]
serial: /dev/serial/by-id/usb-Klipper_rp2040_XXXXXXXXXXXX
restart_method: command

[temperature_sensor TinyFan]
sensor_type: temperature_mcu
sensor_mcu: tinyfan
min_temp: 0
max_temp: 125

[board_pins tinyfan]
mcu: tinyfan
aliases:
    #FAN Ports:
    FAN1_PWM=gpio0, FAN1_RPM=gpio7,
    FAN2_PWM=gpio1, FAN2_RPM=gpio8,
    FAN3_PWM=gpio2, FAN3_RPM=gpio9,
    FAN4_PWM=gpio3, FAN4_RPM=gpio10,

    #AUX Ports:
    AUX1_PWM=gpio4, AUX1_RPM=gpio26,
    AUX2_PWM=gpio5, AUX2_RPM=gpio27,
    AUX3_PWM=gpio6, AUX3_RPM=gpio28,

    #GPIO Header:
    G1=gpio29, G2=gpio11, G3=gpio12,
    G4=gpio13, G5=gpio14, G6=gpio15,

    #Waveshare LED:
    LED=gpio16

[neopixel tinyfan]
pin: tinyfan:LED
initial_RED: 0
initial_GREEN: 1
initial_BLUE: 0




########################
### EXAMPLE CONFIGS: ###
########################



### Octoglasses Example:
#[controller_fan Driver_Z]
#pin: tinyfan:FAN1_PWM
#tachometer_pin: ^tinyfan:FAN1_RPM
#off_below: 0.1
#fan_speed: 1.0
#idle_speed: 0.6
#cycle_time: 0.00004
#hardware_pwm: true
#stepper: stepper_z, stepper_z1, stepper_z2, stepper_z3

#[controller_fan Driver_XYE]
#pin: tinyfan:FAN2_PWM
#tachometer_pin: ^tinyfan:FAN2_RPM
#off_below: 0.1
#fan_speed: 1.0
#idle_speed: 0.6
#cycle_time: 0.00004
#hardware_pwm: true
#stepper: stepper_x, stepper_y, extruder



### Generic FAN Example:
#[fan_generic Noctua1]
#pin: tinyfan:FAN1_PWM
#tachometer_pin: ^tinyfan:FAN1_RPM
#cycle_time: 0.00004
#hardware_pwm: true
#off_below: 0.1



### Nevermore/Bed FAN Example:
# Note: Its better to control the Nevermore with Macros!
#[multi_pin nevermore_fans]
#pins: tinyfan:FAN1_PWM, tinyfan:FAN2_PWM

#[heater_fan Nevermore]
#pin: multi_pin:nevermore_fans
#cycle_time: 0.06    #For Sunon MF50152VX
#cycle_time: 0.01    #For Delta BFB0524HH
#cycle_time: 0.00004 #For 4-Wire Fans
#hardware_pwm: true
#off_below: 0.13
#heater: heater_bed
#heater_temp: 99     #Only for ABS Printing Temps
#fan_speed: 0.6      #At 100% you will get a runout error!



### G-Code Button Example:
#[gcode_button _emergency_stop]
#pin: ^!tinyfan:G1
#press_gcode: {action_emergency_stop(msg)}



### 5v/12v/24v RGB Led Strips on AUX Ports:
# Note: Set the AUX-Jumper to GPIO Mode!
#[output_pin blue]
#pin: tinyfan:AUX1_PWM
#pwm: True
#cycle_time: 0.0005
#hardware_pwm: true

#[output_pin red]
#pin: tinyfan:AUX2_PWM
#pwm: True
#cycle_time: 0.0005
#hardware_pwm: true

#[output_pin green]
#pin: tinyfan:AUX3_PWM
#pwm: True
#cycle_time: 0.0005
#hardware_pwm: true



### Neopixel Example:
# Note: Neopixes need a 100Ohm resistor on G1-6 Pins!
#[neopixel sb_leds]
#pin: tinyfan:G1
#chain_count: 3
#color_order: GRBW

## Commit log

2022-09-01 version 2
    [BOM-tiny-fan.csv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]
2022-09-11 cleanup repo and add useable readme
    [BOM-tiny-fan.csv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]
2022-09-12 fix cad
2022-09-15 Part 1 of 2 from Rama with Love :-)
    Mounts etc
    [BOM-tiny-fan.csv, New_DinClip_M3_Insert.stl, TinyFan_DinRail.stl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]
2022-09-18 Part 2 of 2 from Rama with Love :-)
    Extrusion Mounts were updated, they are now 1mm thicker, because the screw scraped the extrusion before.
    [TinyFan.cfg, TinyFan_Extrusion_1pc_180.ipt, TinyFan_Extrusion_1pc_180.stp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]
2022-09-19 Small Fixes Everywhere
    - Updated images for Consistency
    - Updated Cad Files
    - Updated Example Config
    - Fixes here and there, blahblah :-)
    [TinyFan.cfg, TinyFan_Dinrail_Assembled.iam, TinyFan_Dinrail_BOM.dwg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]
2022-09-19 Config Example Fix
    [TinyFan.cfg]
2022-09-19 Fixes Fixes
    Just some Image updates
    [TinyFan_Pinout.dwg]
2022-09-25 remove thermistor option
    [TinyFan.cfg]
